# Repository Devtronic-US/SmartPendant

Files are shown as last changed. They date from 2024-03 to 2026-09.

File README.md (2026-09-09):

# Devtronic SmartPendant

This project allow to control grblHAL based CNC machine withot PC. It also make work way more convinient.

**Store:** https://devtronic.square.site/

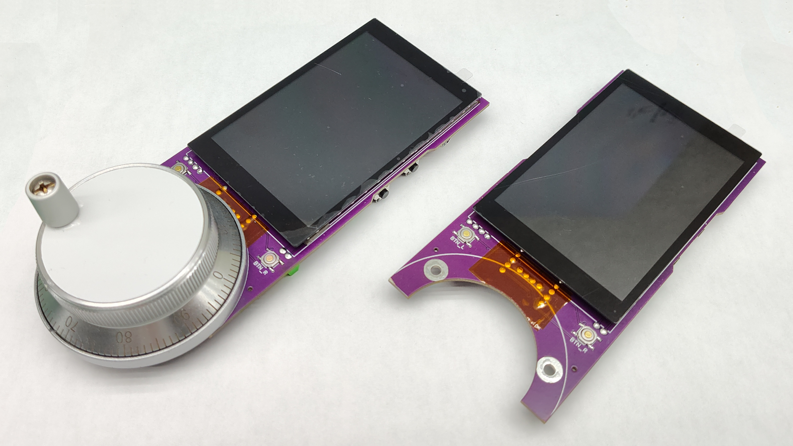
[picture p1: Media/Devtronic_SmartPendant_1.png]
Devtronic SmartPendant

Devtronic SmartPendant

# Case versions

Version that includes "Raft" in the name has solid first layer, all openings have to be open with a knife.
This gives more uniform surface. For front part print it recommended to turn on tree support for encoder opening.

Cable relief should be printed with TPU. After the print, groove have to be opened by cutting and pulling the material.
Cable relief designed for 4 mm cable. If your cable is different - generate new one, function CableReliefCircular(X) accept cable diameter in mm.

# Firmware

Source code for this project can be found there: **https://github.com/nickshl/SmartPendant**

Latest firmware placed in Release folder: [SmartPendant.hex](https://github.com/nickshl/SmartPendant/blob/main/Release/SmartPendant.hex)

To load new firmware [STM32CubeProgrammer](https://www.st.com/en/development-tools/stm32cubeprog.html) is used.
Connect SmartPendant to PC using USB-C cable. Press and hold BOOT0 button, then short press NRST button, couple seconds later BOOT0 button can be released.
Open STM32CubeProgrammer. In top right corner choose "USB" from drop down list.
If field "Port" in "USB Configuration" show "No DFU detected" click update button near it.
Click "Connect" button - STM32CubeProgrammer should establish connection and show current device memory content.
Click "Open File" in left to corner, select firmware HEX file, then click "Download" button in top left corner.
When flashing is done, close STM32CubeProgrammer and short press NRST button on the Controller to restart it. 

**Note:** if flashing is successful, but firmware isn't work, check STM32CubeProgrammer log. If it says "sector 0000 does not exist" erasing operation wasn't successful and new firmware "merged"(write operation can only flip bits from 1 to 0) with old one. To fix this issue, press "eraser" button in bottom right corner and click "Ok" button in pop up window. After erasing is finished "Device memory" should show only FFFFFFFF. Flash new firmware after that. 

# PCB files

Files for PCB version 1.5a can be found in PCB folder which contains Gerber, BOM and Pick and Place files, as well as EasyEDA schematic and PCB json files.

# Parts

To make this project yourself, you will need this essential parts:

* [WeAct BlackPill F411 8M HSE:](https://s.click.aliexpress.com/e/_DC6TlGd)
Note: 25m will work too, but may have problems with entering in bootloader with BOOT button. In this case try to heat up MCU with hair dtyer before trying to enter bootloader mode. If board is programmed, bootload mode can be access by holding MPG button diring power cycle.

* One of this displays:
  [3.5" Display with touchscreen based on ILI9488 LCD controller and FT6236 touch controller](https://www.aliexpress.us/item/3256804935586911.html) - select option ILI9488 FT6236
  [3.5" Display with touchscreen based on ILI9488 LCD controller and FT6236 touch controller](https://www.aliexpress.us/item/3256801122874433.html) - select option ILI9488 FT6236 or IPS ILI9488 FT6236(in my opinion regular looks better)
  [3.5" Display with touchscreen based on ILI9488 LCD controller and FT6236 touch controller](https://www.aliexpress.us/item/3256803764398718.html) - select option ILI9488 FT6236 or IPS ILI9488 FT6236(in my opinion regular looks better)

* [60 mm 6 pin 100 PPR handwheel](https://s.click.aliexpress.com/e/_DCFuJHr)

* [5x5x1.5mm Momentary Panel PCB Surface Mounted Devices SMT Mount 4 Pins Push Button SPST Tactile Tact Switch](https://s.click.aliexpress.com/e/_c3amv5Ub)

* [805 SMD LEDs: green, yellow, red and blue](https://s.click.aliexpress.com/e/_c3RvuM13)

# Case

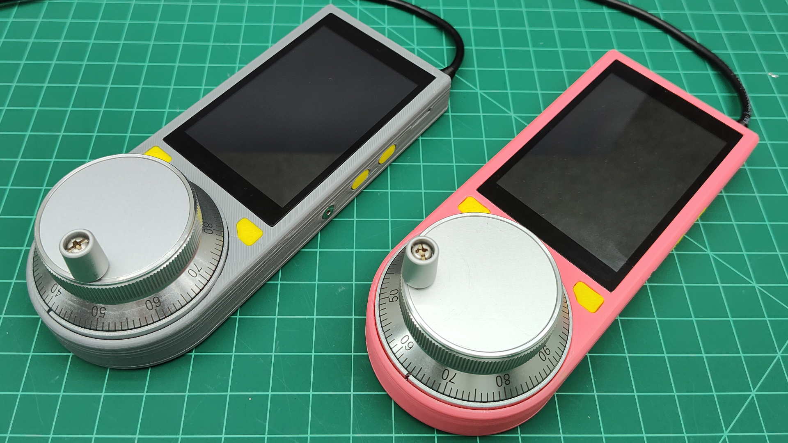
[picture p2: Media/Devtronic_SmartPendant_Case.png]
Devtronic SmartPendant Case


3D_Print folder of this repo contain 3D files(OpenSCAD and STLs) of the case. 

## Dimensions

**160** mm x **65** mm x **20** mm (55 mm with handwheel and handle)
Approx. 6-3/8" x 2-5/8" x 3/4"

# Schematic

Schematic vesion 1.6:
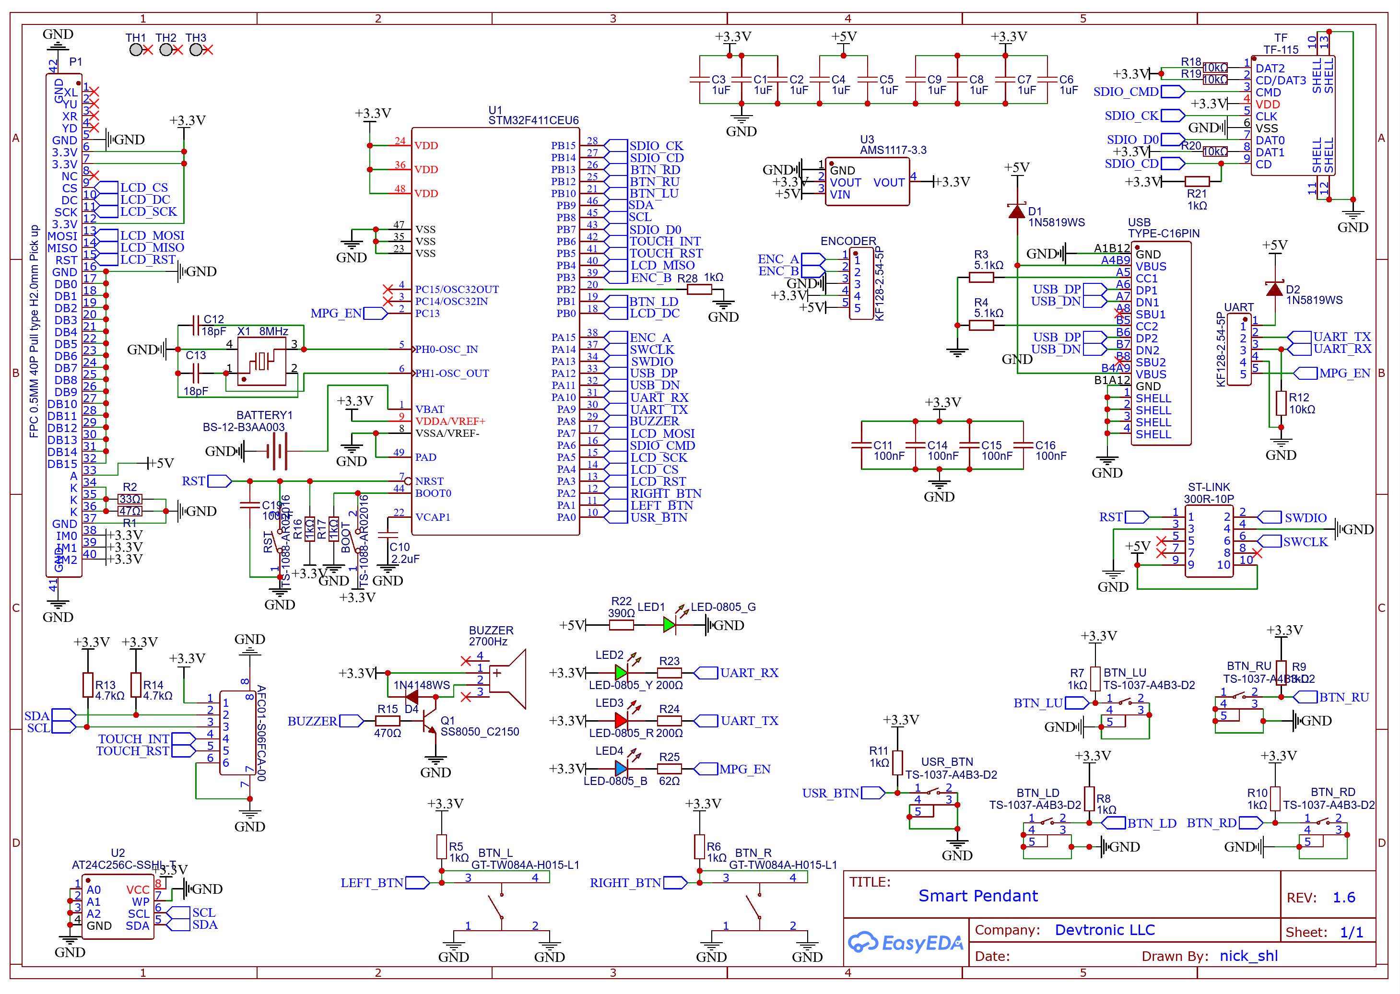
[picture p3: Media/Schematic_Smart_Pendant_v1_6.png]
Devtronic SmartPendant Schematic


Schematic vesion 1.3:
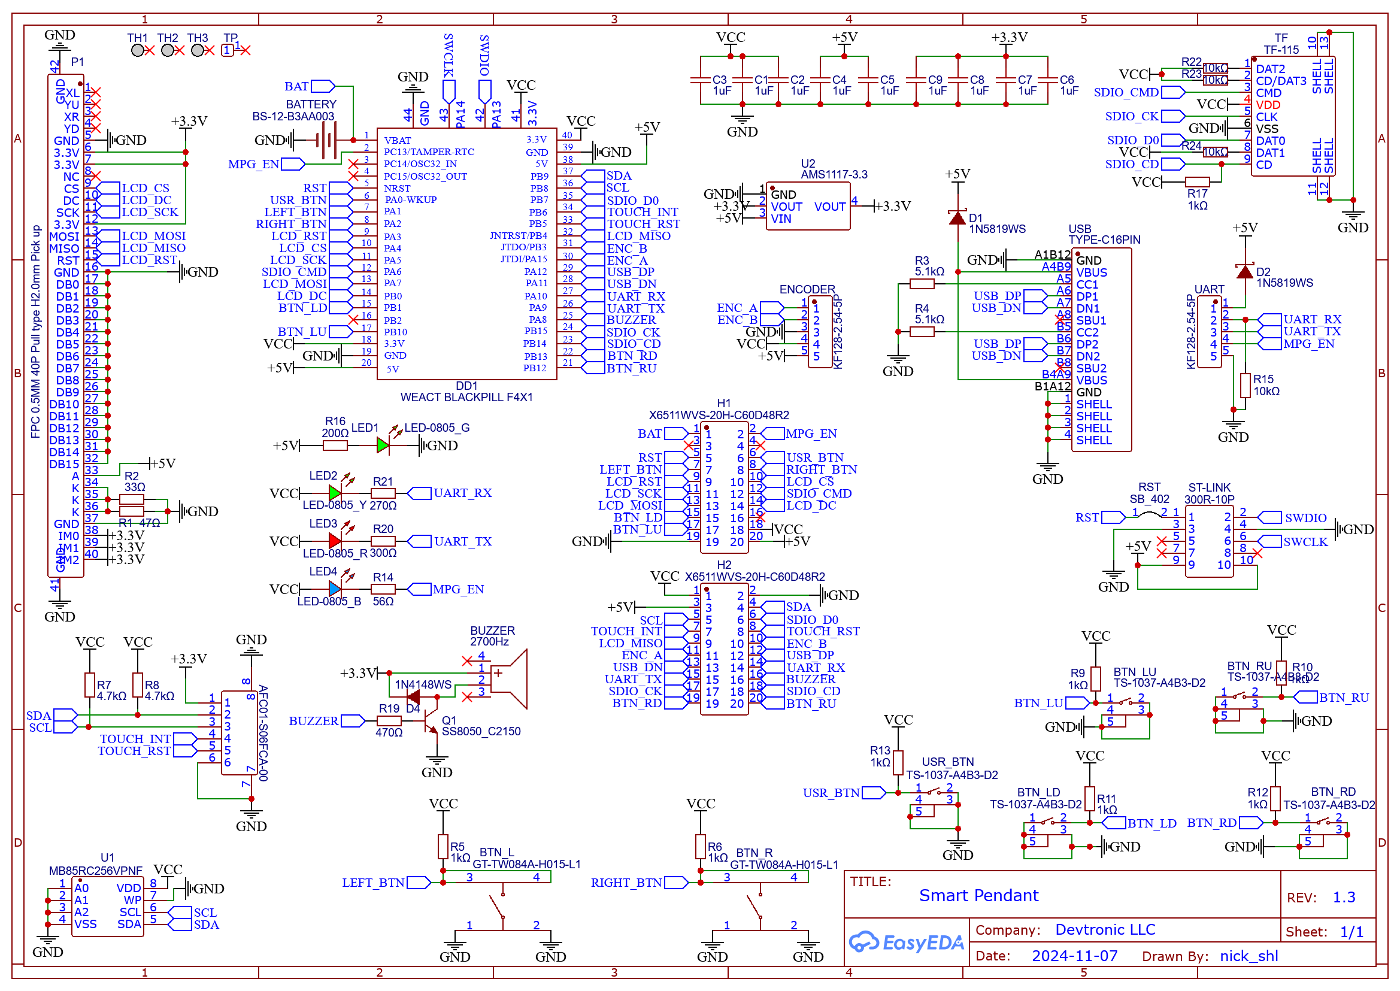
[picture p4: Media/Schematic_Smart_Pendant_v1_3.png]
Devtronic SmartPendant Schematic


Schematic vesion 1.1:
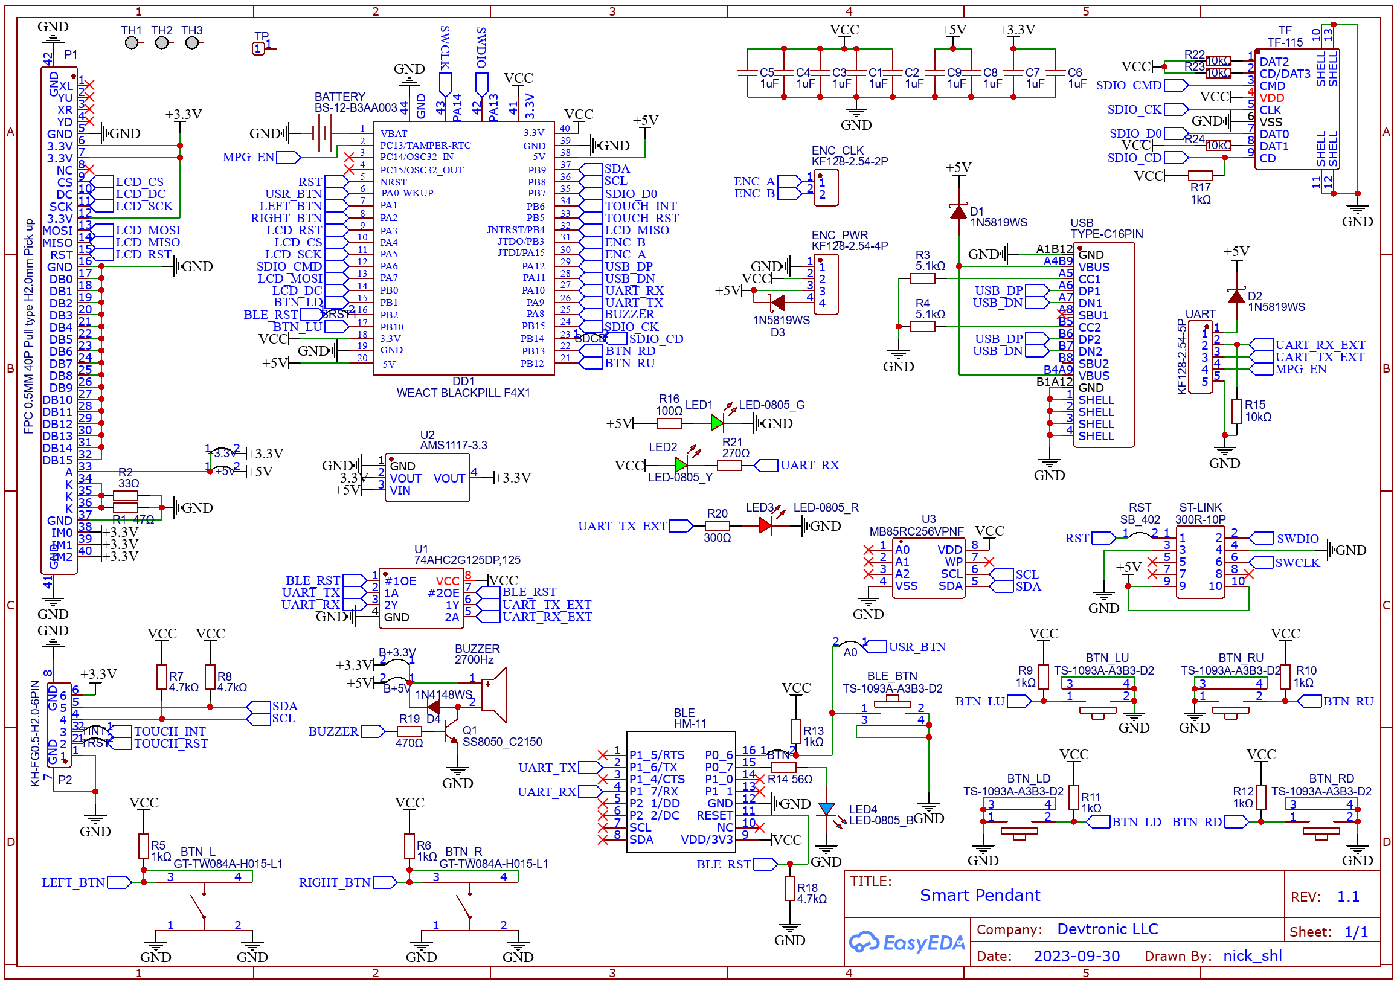
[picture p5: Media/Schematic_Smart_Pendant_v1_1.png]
Devtronic SmartPendant Schematic


# Firmware

Source code and rady to load firmware can be [found there](https://github.com/nickshl/SmartPendant)

# Off the shelf version

It is a possible to assemble pendant from off the helf components with lot of soldering by using this display:

[3.5-inch TFT LCD Module Serial Port SPI Drive ILI9488 with capacitive Touch RGB320 * 480](https://www.aliexpress.us/item/3256804935586911.html)

File SmartPendant_off-the-shelf.scad have code to generate case that was used during prototype stage.

# Assembly instructions videos

English:

English (https://youtu.be/WytGEaL6THc)

Russian:

Russian (https://youtu.be/hrBeEUsN1O0)

# Support

If you really like what I do and want to support my effort, you can do it using this links:

https://github.com/sponsors/nickshl

https://paypal.me/nickshl

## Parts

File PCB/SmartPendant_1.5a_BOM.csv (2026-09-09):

ID | Name | Designator | Footprint | Quantity | Manufacturer Part | Manufacturer | Supplier | Supplier Part | Price
1 | 1N5819WS | D1,D2 | SOD-323_L1.8-W1.3-LS2.5-RD | 2 | 1N5819WS | Hottech(合科泰) | LCSC | C191023 | 0.014
2 | 62Ω | R14 | R0805 | 1 | 0805W8F620JT5E | UNI-ROYAL(厚声) | LCSC | C17784 | 0.004
3 | 390Ω | R16 | R0805 | 1 | 0805W8F3900T5E | UNI-ROYAL(厚声) | LCSC | C17655 | 0.003
4 | 200Ω | R20,R21 | R0805 | 2 | 0805W8F2000T5E | UNI-ROYAL(厚声) | LCSC | C17540 | 0.007
5 | BS-12-B3AA003 | BATTERY | BAT-SMD_BS-12-B3AA011 | 1 | BS-12-B3AA003 | MYOUNG(美阳) | LCSC | C964723 | 0.194
6 | FPC 0.5MM 40P Pull type H2.0mm Pick up | P1 | CONN-SMD_AFC07-S40ECC-00 | 1 | AFC07-S40ECC-00 | JS(钜硕电子) | LCSC | C11097 | 0.209
7 | AT24C256C-SSHL-T | U1 | SOIC-8_L4.9-W3.9-P1.27-LS6.0-BL | 1 | AT24C256C-SSHL-T | MICROCHIP(美国微芯) | LCSC | C6482 | 0.379
8 | TYPE-C16PIN | USB | USB-C-SMD_TYPE-C16PIN | 1 | TYPE-C16PIN | SHOU HAN(首韩) | LCSC | C393939 | 0.062
9 | 1uF | C1,C2,C3,C4,C5,C6,C7,C8,C9 | C0805 | 9 | CL21B105KBFNNNE | SAMSUNG(三星) | LCSC | C28323 | 0.044
10 | AFC01-S06FCA-00 | P2 | FPC-SMD_P0.50-6P_AFC01-S06FCA-00 | 1 | AFC01-S06FCA-00 | JS(钜硕电子) | LCSC | C262655 | 0.102
11 | 2700Hz | BUZZER | BUZ-SMD_4P-L7.5-W7.5-P7.59-TL | 1 | MLT-7525 | 华能 | LCSC | C95299 | 0.239
12 | TS-1037-A4B3-D2 | USR_BTN,BTN_RU,BTN_LD,BTN_RD,BTN_LU | KEY-SMD_2P-L7.1-W7.1-P4.00-LS9.0 | 5 | TS-1037-A4B3-D2 | Yuandi(元迪) | LCSC | C499324 | 0.133
13 | KF128-2.54-5P | ENCODER,UART | CONN-TH_5P-P2.54_KF128-2.54-5P | 2 | KF128-2.54-5P | KEFA(科发) | LCSC | C474923 | 0.579
14 | 1kΩ | R5,R13,R9,R10,R11,R12,R17,R6 | R0805 | 8 | 0805W8F1001T5E | UNI-ROYAL(厚声) | LCSC | C17513 | 0.004
15 | 4.7kΩ | R7,R8 | R0805 | 2 | 0805W8F4701T5E | UNI-ROYAL(厚声) | LCSC | C17673 | 0.005
16 | WEACT BLACKPILL F4X1 | DD1 | BLACKPILL_V31_SMD | 1
17 | X6511WVS-20H-C60D48R2 | H1,H2 | HDR-SMD_20P-P2.54-V-M-LS4.8_XKB_R2 | 2 | X6511WVS-20H-C60D48R2 | XKB Connection(中国星坤) | LCSC | C2883777 | 0.567
18 | 10kΩ | R24,R22,R23,R15 | R0805 | 4 | 0805W8F1002T5E | UNI-ROYAL(厚声) | LCSC | C17414 | 0.004
19 | 470Ω | R19 | R0805 | 1 | 0805W8F4700T5E | UNI-ROYAL(厚声) | LCSC | C17710 | 0.005
20 | 1N4148WS | D4 | SOD-323_L1.8-W1.3-LS2.5-RD | 1 | 1N4148WS | CJ(江苏长电/长晶) | LCSC | C2128 | 0.018
21 | SS8050_C2150 | Q1 | SOT-23-3_L2.9-W1.3-P1.90-LS2.4-BR | 1 | SS8050 | CJ(江苏长电/长晶) | LCSC | C2150 | 0.019
22 | TF-115 | TF | TF-SMD_TF-115 | 1 | TF-115 | XUNPU(讯普) | LCSC | C266620 | 0.174
23 | 47Ω | R1 | R0805 | 1 | 0805W8F470JT5E | UNI-ROYAL(厚声) | LCSC | C17714 | 0.005
24 | 5.1kΩ | R3,R4 | R0805 | 2 | 0805W8F5101T5E | UNI-ROYAL(厚声) | LCSC | C27834 | 0.007
25 | 33Ω | R2 | R0805 | 1 | 0805W8F330JT5E | UNI-ROYAL(厚声) | LCSC | C17634 | 0.005
26 | AMS1117-3.3 | U2 | SOT-223-3_L6.5-W3.4-P2.30-LS7.0-BR | 1 | AMS1117-3.3 | AMS | LCSC | C6186 | 0.22
27 | LED-0805_G | LED1 | LED0805_GREEN | 1 | NCD0805G1 | 国星光电 |  | C84260 | 0.023
28 | LED-0805_Y | LED2 | LED0805_GREEN | 1 | NCD0805G1 | 国星光电 |  | C84260 | 0.023
29 | LED-0805_B | LED4 | LED0805_BLUE | 1 | D-B080508B1-KS2 | 方舟 ARKLED |  | C108412 | 0.02
30 | LED-0805_R | LED3 | LED0805_RED | 1 | 17-21SURC/S530-A3/TR8 | EVERLIGHT(台湾亿光) |  | C72037 | 0.025
31 | GT-TW084A-H015-L1 | BTN_L,BTN_R | SW-SMD_4P-L5.2-W5.2-P3.70-LS6.4-BL | 2 | GT-TW084A-H015-L1 | G-Switch(品赞) | LCSC | C7425483 | 0.034

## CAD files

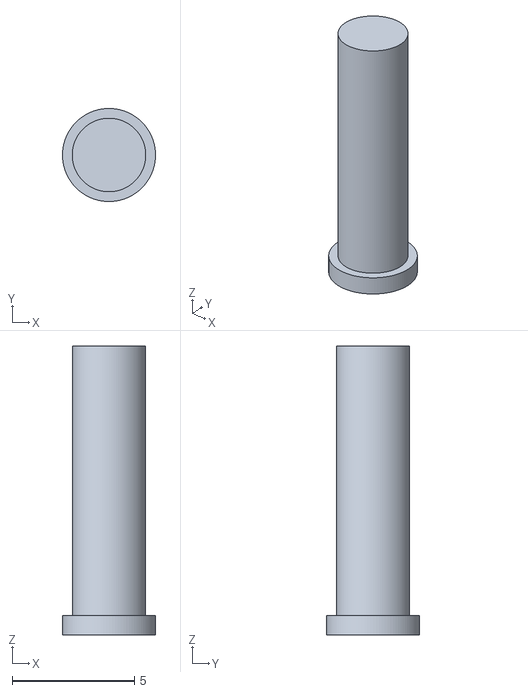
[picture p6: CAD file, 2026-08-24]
3D_Print/Pendant_Back_Buttons_v1_6.stl
3.80 x 3.80 x 11.8

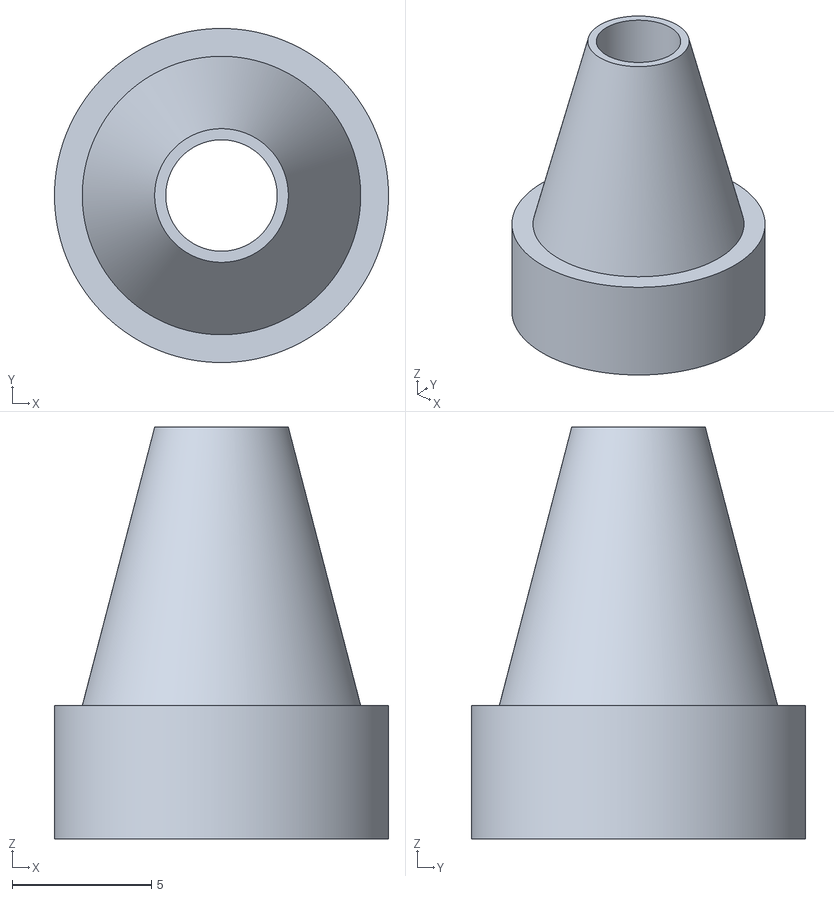
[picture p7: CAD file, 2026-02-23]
3D_Print/SmartPendant_Cable_Relief.stl
12.0 x 12.0 x 14.8

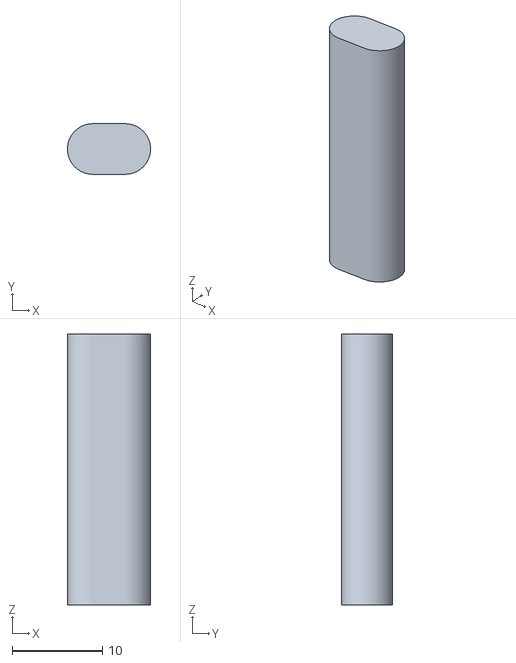
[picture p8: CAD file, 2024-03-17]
3D_Print/Pendant_Side_Button_Jig.stl
9.20 x 5.60 x 30.0

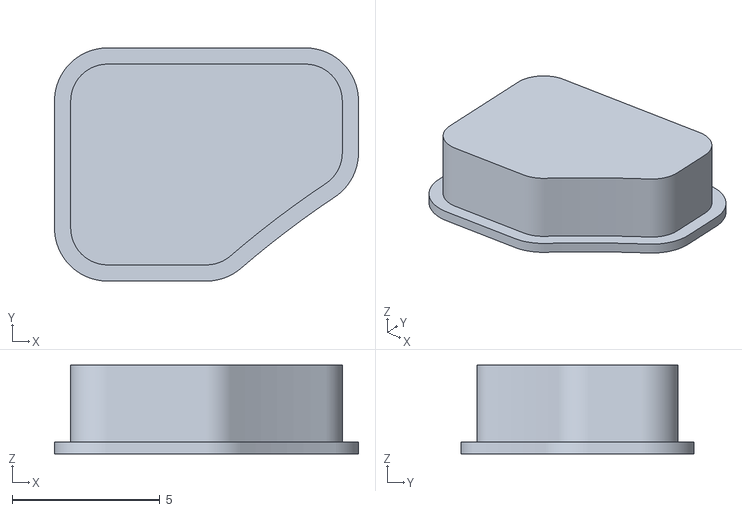
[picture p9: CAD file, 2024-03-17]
3D_Print/Pendant_Front_Button_Left.stl
10.3 x 7.90 x 3.00

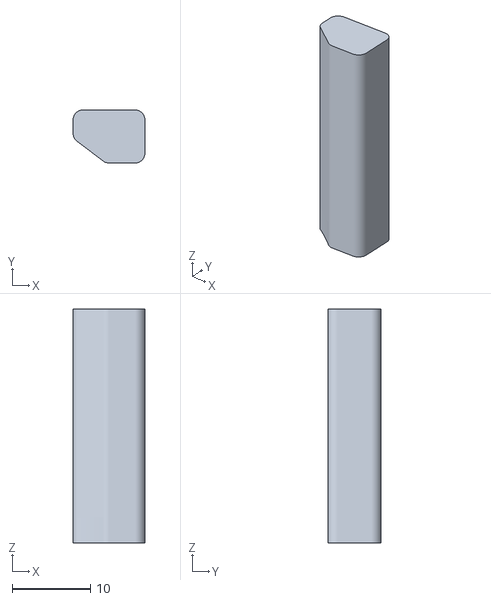
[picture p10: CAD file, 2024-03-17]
3D_Print/Pendant_Front_Button_Jig.stl
9.20 x 6.80 x 30.0

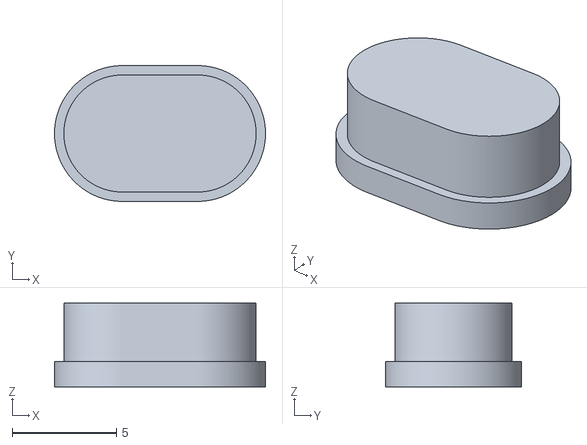
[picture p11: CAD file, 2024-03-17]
3D_Print/Pendant_Side_Button.stl
10.1 x 6.50 x 4.00

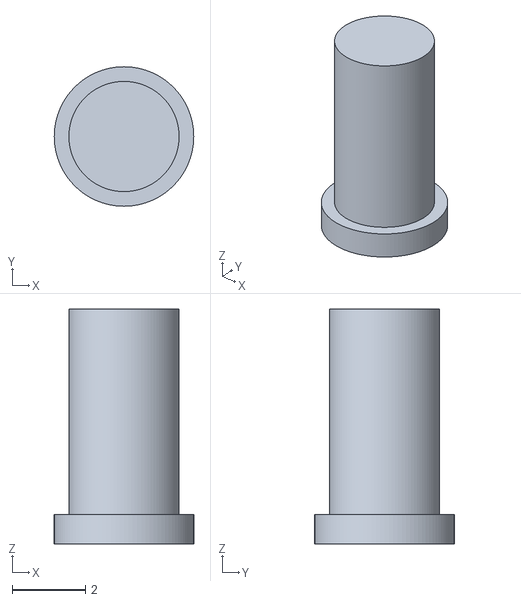
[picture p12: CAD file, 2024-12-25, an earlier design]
3D_Print/Pendant_Back_Buttons_v1_3.stl
3.80 x 3.80 x 6.40

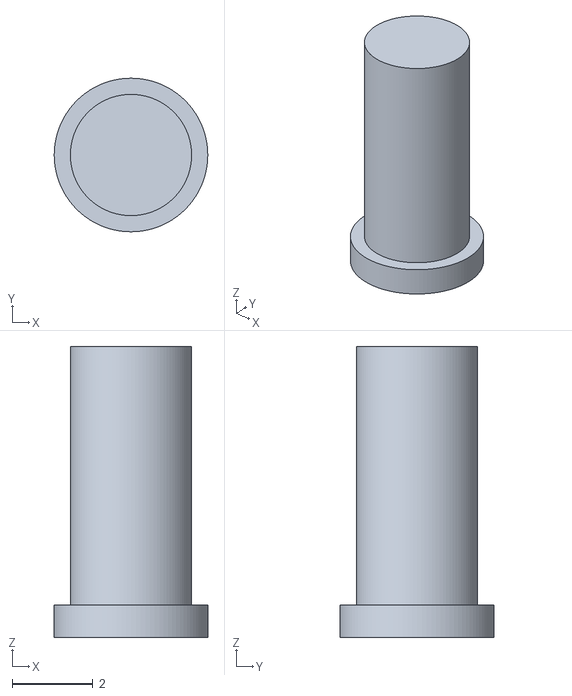
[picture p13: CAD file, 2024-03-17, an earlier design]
3D_Print/Pendant_Back_Buttons.stl
3.80 x 3.80 x 7.20

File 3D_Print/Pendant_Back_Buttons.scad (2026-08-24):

$fn=100;

// Possible options(affect back panel only):
// 1.5 or less    - For versions with blackpill on the board
// 1.6 or greater - For version without blackpill
VERSION = 1.6;

// Generation code
if(VERSION < 1.6)
{
  cylinder(d=3, h=6.4);
  cylinder(d=3.8, h=0.8);
}
else
{
  cylinder(d=3, h=11.8);
  cylinder(d=3.8, h=0.8);
}

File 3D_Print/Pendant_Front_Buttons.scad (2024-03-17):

$fn = 300;

//mirror([1,0,0])

// First parameter - corner radius. It can be less than original one for clearence.
// Second parameter - Radius for lock, it may be greater than original
// Third parameter - length reduction(added to clearence gained by smaller first parameter)
FrontButton(2.5, 3.6, 0.3);

//Jig(2.5, 3.6, 0.3, 30);

// *******************************************************************
// ***   Button Hole   ***********************************************
// *******************************************************************
module FrontButton(DB, DL, LR)
{
  // All parameters from Pendant
  DFG = 2.8;
  D = 3;
  SW = 55.3; // Screen width
  SH = 88.9; // Screen height
  BW = 60; // Board Width
  BL = 126; // Board Length(from center of encoder to top edge)
  ED = BL - BW/2 - SH - (BW - SW)/2;
  W = 60; // Width(encoder & board)
  T = 2.4; // Case thickness
  
  H = 3;
  R = W/2+H+D/2;

  Y1 = (W/2+ED-DFG) - ((W/2+ED-DFG)-28.3)*2 + D/2; // Fid simmetrical bottom distance
  X1 = sqrt(abs(Y1*Y1 - R*R));
  X2 = SW/2 - (SW/2-23.4)*2;// + D/2;
  Y2 = sqrt(abs(X2*X2 - R*R));

  difference()
  {
    hull()
    {
      translate([X1,Y1,-0.1]) cylinder(d=DB, h=3);
      translate([X2,Y2,-0.1]) cylinder(d=DB, h=3);
      translate([SW/2-D/2 - LR,Y1,-0.1]) cylinder(d=DB, h=3);
      translate([SW/2-D/2 - LR,W/2+ED-DFG-D/2,-0.1]) cylinder(d=DB, h=3);
      translate([X2,W/2+ED-DFG-D/2,-0.1]) cylinder(d=DB, h=3);
    }
    translate([0,0,-0.2]) cylinder(d=W+H*2+(D-DB), h=3+0.4);
  }
  difference()
  {
    hull()
    {
      translate([X1,Y1,-0.1]) cylinder(d=DL, h=0.4);
      translate([X2,Y2,-0.1]) cylinder(d=DL, h=0.4);
      translate([SW/2-D/2 - LR,Y1,-0.1]) cylinder(d=DL, h=0.4);
      translate([SW/2-D/2 - LR,W/2+ED-DFG-D/2,-0.1]) cylinder(d=DL, h=0.4);
      translate([X2,W/2+ED-DFG-D/2,-0.1]) cylinder(d=DL, h=0.4);
    }
    translate([0,0,-0.2]) cylinder(d=W+H*2-(DL-D), h=3+0.4);
  }
}

// *******************************************************************
// ***   Button Hole   ***********************************************
// *******************************************************************
module Jig(DB, DL, LR, HEIGHT)
{
  // All parameters from Pendant
  DFG = 2.8;
  D = 3;
  SW = 55.3; // Screen width
  SH = 88.9; // Screen height
  BW = 60; // Board Width
  BL = 126; // Board Length(from center of encoder to top edge)
  ED = BL - BW/2 - SH - (BW - SW)/2;
  W = 60; // Width(encoder & board)
  T = 2.4; // Case thickness
  
  H = 3;
  R = W/2+H+D/2;

  Y1 = (W/2+ED-DFG) - ((W/2+ED-DFG)-28.3)*2 + D/2; // Fid simmetrical bottom distance
  X1 = sqrt(abs(Y1*Y1 - R*R));
  X2 = SW/2 - (SW/2-23.4)*2;// + D/2;
  Y2 = sqrt(abs(X2*X2 - R*R));

  difference()
  {
    hull()
    {
      translate([X1,Y1,-0.1]) cylinder(d=DB, h=HEIGHT);
      translate([X2,Y2,-0.1]) cylinder(d=DB, h=HEIGHT);
      translate([SW/2-D/2 - LR,Y1,-0.1]) cylinder(d=DB, h=HEIGHT);
      translate([SW/2-D/2 - LR,W/2+ED-DFG-D/2,-0.1]) cylinder(d=DB, h=HEIGHT);
      translate([X2,W/2+ED-DFG-D/2,-0.1]) cylinder(d=DB, h=HEIGHT);
    }
    translate([0,0,-0.2]) cylinder(d=W+H*2+(D-DB), h=H+0.4);
  }
}

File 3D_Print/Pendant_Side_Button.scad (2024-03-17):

$fn = 300;

SideButton(9.2, 5.6, 6.5); // 1
//SideButton(9, 5.4, 6.5); // 2

//Jig(9.2, 5.6, 6.5, 30);

// *******************************************************************
// ***   SideButton module   *****************************************
// *******************************************************************
module SideButton(L, DB, DL)
{
  // Button
  hull()
  {
    translate([-(L-DB)/2,0,0]) cylinder(d=DB, h=4);
    translate([+(L-DB)/2,0,0]) cylinder(d=DB, h=4);
  }
  // Button base
  hull()
  {
    translate([-(L-DB)/2,0,0]) cylinder(d=DL, h=4-2.8);
    translate([+(L-DB)/2,0,0]) cylinder(d=DL, h=4-2.8);
  }
}

// *******************************************************************
// ***   Jig module   ************************************************
// *******************************************************************
module Jig(L, DB, DL, H)
{
  // Button
  hull()
  {
    translate([-(L-DB)/2,0,0]) cylinder(d=DB, h=H);
    translate([+(L-DB)/2,0,0]) cylinder(d=DB, h=H);
  }
}

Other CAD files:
3D_Print/Pendant_Front_Button_Right.stl
3D_Print/SmartPendant.scad
3D_Print/SmartPendant_off-the-shelf.scad

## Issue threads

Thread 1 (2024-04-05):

Ссылка на повтор заказа

how-eee, 2024-04-05:
Привет. А есть ли ссылка на готовый заказ на jlcpcb?
Чтобы заново гербер и файлы сверления и пик анд плейс не кидать, чтобы их инженера опять не проверяли всё. Не брали денег за обработку.
Если есть такая возможность, дай пожалуйста готовыйпроект, чтобы только заново заказать. Я никогда там не заказывал и нет времени разбираться. Продам платы и тебе закину половину за разработку. Спасибо большое за опен проект! Респект!

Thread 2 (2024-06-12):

no display output

T4KUUY4, 2024-06-12:
Hi,
I just finished building your Pendant and I sadly cannot get the smartpendant.hex onto the weAct.
Im trying to flash it via DFU in STM32CubeProg. After flashing, nothing happens on the display etc.
So i read the chip again, and its completely different.
I then flashed with verify on, and it immediatly failed the verification after flashing.

Any ideas how i can fix that?

Thanks in Advance,
Tom

T4KUUY4, 2024-06-12:
Seems like i managed to get the firmware on after chip erasing.
But sadly no screen output. Does it need to be connected to anything or does 5V usb already show the screen?

T4KUUY4, 2024-06-12:
Update. i seem to be stuck in a bootloader loop when flashing your premade hex file.
I cannot exit it. If i click the key button, i can toggle the LED. but i cant hold to exit.

Closed 2024-06-16.

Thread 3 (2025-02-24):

3D models do not import in Bambu Studio.

phil-barrett, 2025-02-24:
None of the 3D files import to Banbu Studio.  Trying to import them into FreeCAD 1.0 fails silently (nothing loaded). The screen shot below was from trying to load Pendant.stl but all of the .stl files have the same error.

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

phil-barrett, 2025-02-24:
Also, trying to import the stl files into VCarve Pro, it gets stuck at 0% for a long time.

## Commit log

2024-03-17 Initial version
    [Pendant.scad, Pendant_Back.scad, Pendant_Back_Buttons.scad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]
2024-12-25 Case update
    [Pendant.scad, Pendant_Back.scad, Pendant_Back_Buttons.scad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]
2024-12-27 Added schematic for PCB 1.3
2025-01-12 Back cover fix for version 1.3
    [Pendant_Back.scad]
